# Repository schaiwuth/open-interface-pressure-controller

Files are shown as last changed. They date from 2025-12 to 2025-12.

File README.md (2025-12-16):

# Open-interface Programmable Pressure Controller

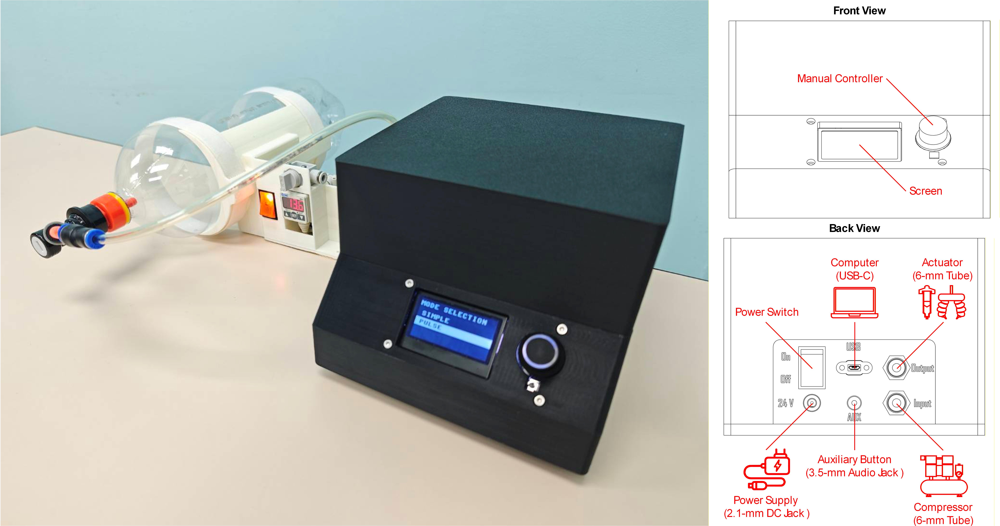
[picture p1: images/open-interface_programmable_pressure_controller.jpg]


An open-source programmable pressure controller designed for pneumatic actuation in robotics and automation. This device enables computer-controlled air pressure output in real time, through a serial communication protocol. With a built-in manual controller, it also supports stand-alone operation. The controller can be operated from any platform capable of serial communication, making it compatible with a wide range of robotics and automation frameworks. This open-interface design allows the system to be easily adapted and integrated into unique or custom robotic applications.

## Key Specifications

| Parameter | Specifications |
|---|:---:|
| Fluid Type | Air |
| Set Pressure | 0–900 kPa |
| Power Supply | 24 VDC, 0.4 A |
| Max Frequency | 10 Hz |
| Programming Protocol | Serial Communication (Baud Rate: 115200) |
| Dimension (WxLxH) | 185x236.2x150 mm |
| Weight (kg) | 1.35 |

## Instruction Manual

The instruction manual for the pressure controller is available [here](instruction_manual.pdf).

For device installation, several steps need to be done:
* Connect a 24-VDC power supply to the DC jack connector (5.5 × 2.1 mm). This power line routes through a rocker switch, functioning as the power switch.
* Connect a pressure source, such as a compressor or air tank, via the 6-mm pneumatic input  port.
* Connect a pneumatic actuator via the 6-mm pneumatic output port.
* (Optional) Connect a computer via the USB-C port for programable operation.
* (Optional) Connect an external button via the 3.5-mm jack connector for auxiliary control during manual operation.

## List of Main Components

* [Pi Interface](https://github.com/Ninth2234/Pi_Interface) x1
* ET-MINI I2C D/A x1
* SMC ITV2050-31 x1
* SMC VT307-5G x1
* Cytron UC00C x1
* Single-channel Relay 3.3 V x1
* [Chassis](cad_models/chassis.stl) x1
* [Cover](cad_models/cover.stl) x1
* [Interface Panel](cad_models/interface_panel.stl) x1
* Adafruit 4056 x1
* Rocker Switch x1
* DC Jack Female 5.5x2.1 mm x1
* Audio Jack Female 3.5 mm x1
* SMC KQ2E06 x2

## Programming Commands

Programming commands are flexibly defined and can be modified with the modification in the firmware level. Default commands include:

| Commands | Descriptions |
|:---:|---|
| vers | Report the firmware version |
| home | Reset all parameters to default values and return to mode selection. |
| mode | Read or set the system mode.<br> • Reading: mode<br> • Setting to “simple”: mode=simple |
| pres | Read the feedback value of control pressure in kPa. |
| pref | Read or set the value of set pressure.<br> • Reading: pref<br> • Setting to 100 kPa: pref=100 |
| pmax | Read or set the max value of set pressure.<br> • Reading: pmax<br> • Setting to 500 kPa: pmax=500 |
| offs | Zero the current feedback value of control pressure.|
| oupt | Read or set the state of output pressure, in “simple” mode, and output pressure pulses, in “pulse” mode.<br> • Reading: oupt<br> • Setting to "on": oupt=on<br><br> In “simple” mode, the state “on” controls output pressure to set pressure. The state “off” neutralizes output pressure. On the other hand, in “pulse” mode, the state “on” generates the pulses with output pressure controlled to set pressure. The state “off” stops the pulses and neutralizes output pressure.|
| freq | Read or set the frequency of output pulses. Available only in “pulse” mode.<br> • Reading: freq<br> • Setting to 2 Hz: freq=2 |

## Manual Commands

This device also supports manual operation for stand-alone use. There are three types of button presses for controlling the pressure controller: single press, double press, and press and hold.

| Commands | Descriptions |
|:---:|---|
| single press | In mode selection, enter the highlighted system mode.<br><br> In “simple” and “pulse” mode, toggle the output state. |
| double press | Change the adjusting parameter to the next item on the list. |
| press and hold | Reset all parameters to default values and return to mode selection. |

## Wiring Diagram

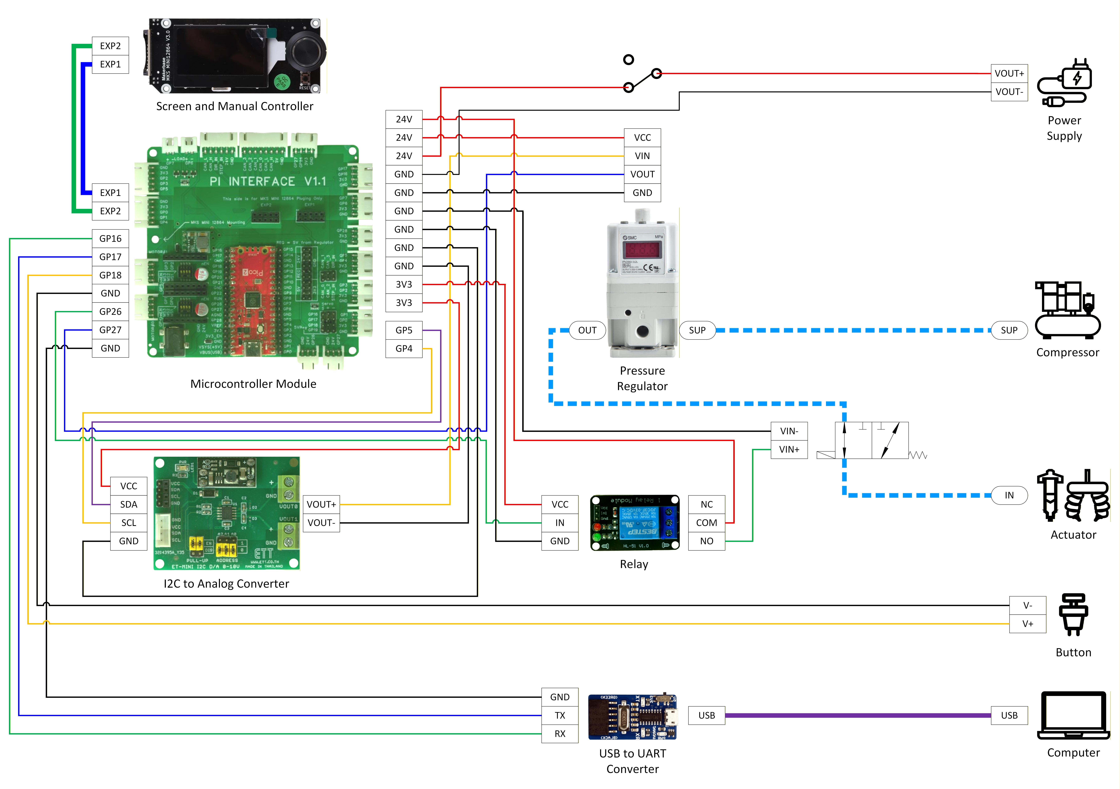
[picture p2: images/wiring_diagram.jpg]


## Firmware

The firmware for this device is developed in MicroPython, and its repository can be found [here](https://github.com/Ninth2234/Pi_Interface).

## Video Demonstration

* [Manual Pulse-mode Operation on a Soft Pneumatic Actuator](https://www.youtube.com/watch?v=VrCpQ_EVPBg)

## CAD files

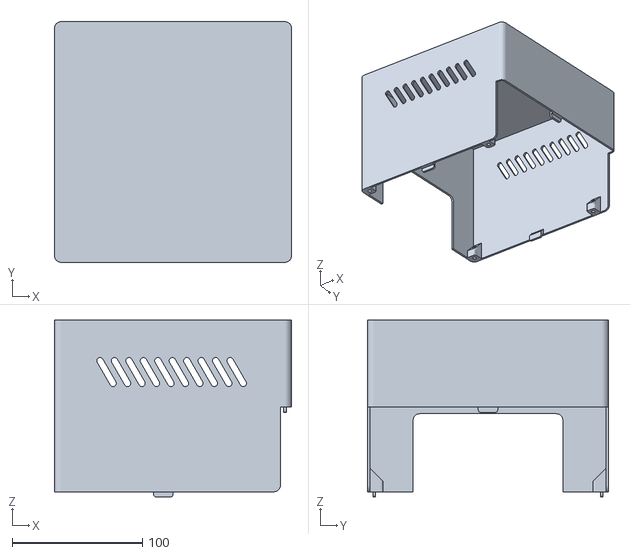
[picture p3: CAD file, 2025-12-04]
cad_models/cover.stl
182.1 x 185.0 x 136.0

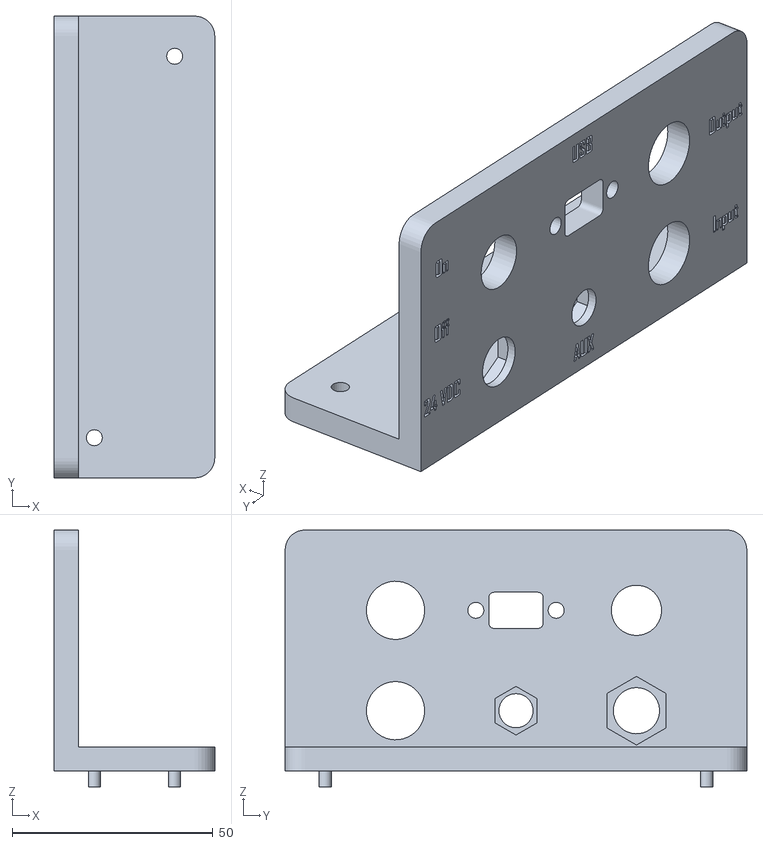
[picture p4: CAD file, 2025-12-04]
cad_models/interface_panel.stl
40.0 x 115.0 x 64.0

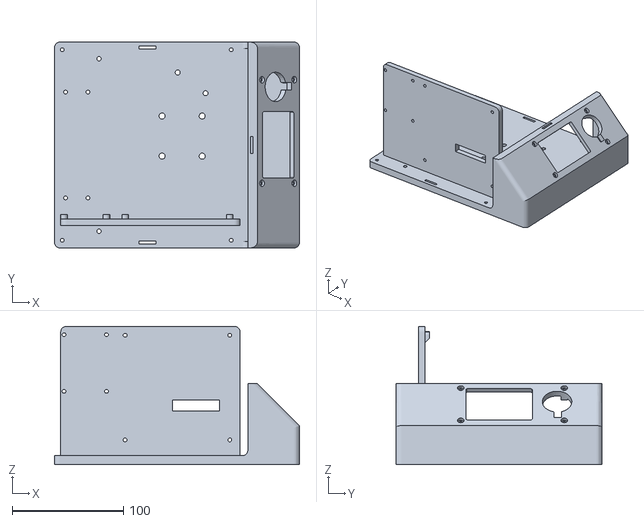
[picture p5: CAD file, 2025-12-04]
cad_models/chassis.stl
220.0 x 185.0 x 124.2

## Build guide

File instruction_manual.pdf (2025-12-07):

### Instruction Manual for

### Open-interface Programmable

### Pressure Controller

The intended use of this product is to enable programmable control of pneumatic air pressure through a user-defined computer program via serial communication.

## User Interface

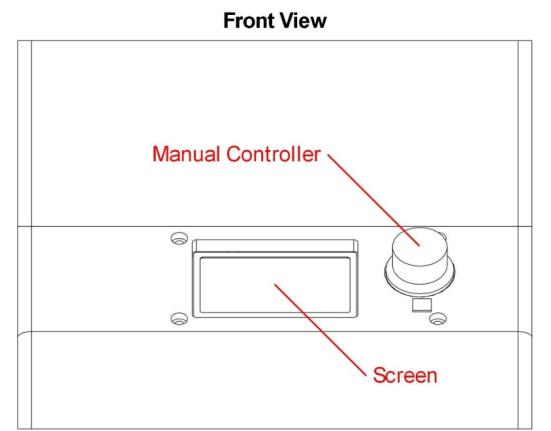
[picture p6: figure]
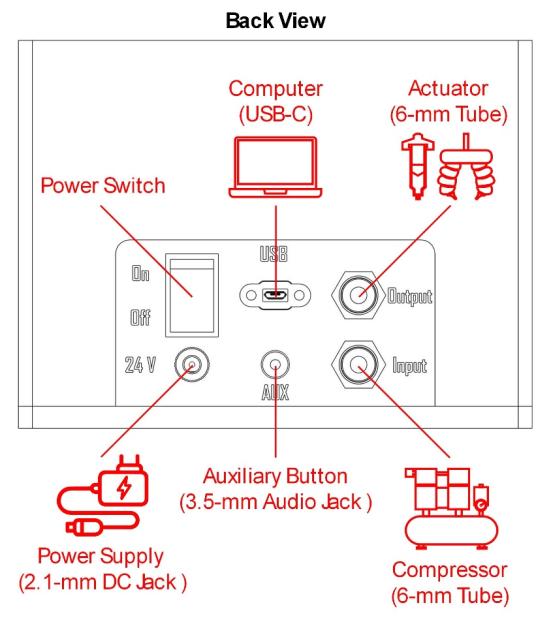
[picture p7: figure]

## Key Specifications

Fluid Type | Air
Set Pressure | 0–900 kPa*
Supply Pressure | Set Pressure + 100 kPa
Power Supply | Voltage | 24 VDC
| Current | 0.4 A
Total Accuracy | | ±1.225% FS
Max Frequency | | 10 Hz
Temperature | | 0–50 °C
Programming Protocol | | Serial Communication (Baud Rate: 115200)

## Manual Pressing

Actions | Descriptions
single press | In mode selection, enter the highlighted system mode. In “simple” mode, toggle the state of output pressure. The state “on” controls output pressure to set pressure. Otherwise, the state “off” neutralizes output pressure. In “pulse” mode, toggle the state of output pressure pulses. The state “on” generates the pulses with output pressure controlled to set pressure. Otherwise, the state “off” stops the pulses and neutralizes output pressure. During the state “on”, the screen turns green.
double press | Change the adjusting parameter to the next item on the list.
press and hold | Reset all parameters to default values and return to mode selection.

## Programming Commands / Responses

Commands | Descriptions
vers | Report the firmware version.
home | Reset all parameters to default values and return to mode selection.
mode | Read or set the system mode. • Reading: mode • Setting to “simple”: mode=simple
pres | Read the feedback value of control pressure in kPa.
pref | Read or set the value of set pressure. • Reading: pref • Setting to 100 kPa: pref=100
pmax | Read or set the max value of set pressure. • Reading: pmax • Setting to 500 kPa: pmax=500
offs | Zero the current feedback value of control pressure.
oupt | Read or set the state of output pressure, in “simple” mode, and output pressure pulses, in “pulse” mode. • Reading: oupt • Setting to “on”: oupt=on
freq | Read or set the frequency of output pulses. Available only in “pulse” mode. • Reading: freq • Setting to 2 Hz: freq=2
ok | Response for successful recognition and execution of a command.
unrecognized command | Response for invalid commands

* When set pressure is set to be 0–5 kPa, it is uncontrollable. If this value falls in this range, the controller turns it to 5 kPa.

For additional details, please visit the product repository (github.com/schaiwuth/open-interface-pressure-controller).

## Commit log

2025-12-03 Add CAD models and images.
    [chassis.stl, cover.stl, interface_panel.stl]
2025-12-04 Update CAD models
    [chassis.stl, cover.stl, interface_panel.stl]
2025-12-16 Update readme and wiring diagram
2025-12-23 Update wiring diagram
